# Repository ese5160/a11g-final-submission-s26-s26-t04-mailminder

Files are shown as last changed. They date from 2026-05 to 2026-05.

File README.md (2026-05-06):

Review Assignment Due Date (https://classroom.github.com/a/Y5lYn2wb)

# a11g-final-submission

**Team Number:4**

**Team Name:MailMinder**

| Team Member Name | Email Address | GitHub Username |
| --- | --- | --- |
| Haoliang Xie | liang027@seas.upenn.edu | socold729 |
| Yubin Guan | guan1@seas.upenn.edu | guan1112  |

**GitHub Repository URL: https://github.com/ese5160/a11g-final-submission-s26-s26-t04-mailminder
Git website:https://ese5160.github.io/a11g-final-submission-s26-s26-t04-mailminder**

## 1. Video Presentation
https://youtu.be/0NLSgTLzU24?si=XQApfhHq24TX3WXG

## 2. Project Summary
- Give a 2 sentence description of your device.
  MailMinder is a smart mailbox system built around the SiWG917 Cortex-M4 microcontroller with a custom-designed PCBA, FreeRTOS-based firmware, and cloud connectivity. It detects mail delivery, monitors mailbox security, and allows both local and remote access through keypad input, MQTT communication, and a Node-RED dashboard.
- What inspired you to do the project? What problem is your device solving?
The mailbox in my apartment does not provide any notification when new mail arrives, so we have to check it in person regularly. I often forget to do that, which leads to mail accumulating and sometimes missing important letters.
- How do you use the Internet to augment your device functionality?
The mailbox connects to the cloud through MQTT over TLS, which enables secure two-way communication between the device and a Node-RED dashboard. This Internet connection allows remote unlock commands, temporary passcode updates, real-time status reporting, alert notifications, and OTA firmware updates.
- Explain how your Internet-connected device is designed.
  MailMinder is built as a layered embedded system with custom hardware, FreeRTOS firmware, and cloud integration. On the hardware side, we designed and fabricated a custom PCB centered on the SiWG917 Cortex-M4 MCU and integrated multiple sensors, a keypad, a display, and an electronic lock actuator. On the firmware side, we implemented a multitasking architecture using FreeRTOS, where different tasks handle sensing, local user input, state management, actuator/display control, cloud messaging, and OTA support. On the cloud side, the device communicates with a Node-RED dashboard over MQTT, allowing the mailbox to synchronize status and receive remote commands.
- Include sensors, actuators, and other critical components.
  The system includes several key sensing and control components:
    - IR sensor for mail delivery detection
    - FSR for confirming mail insertion events
    - Reed switch for mailbox door open/close detection
    - IMU for tamper detection and physical disturbance monitoring
    - Matrix keypad for local PIN entry and user interaction
    - Servo/electronic lock for secure locking and unlocking
    - LCD display for local status feedback
    - Wi-Fi / MQTT stack on the SiWG917 for Internet connectivity
    - Custom-designed PCB/PCBA for integrating all system modules into a single embedded platform
- Include your system-level block diagram here.
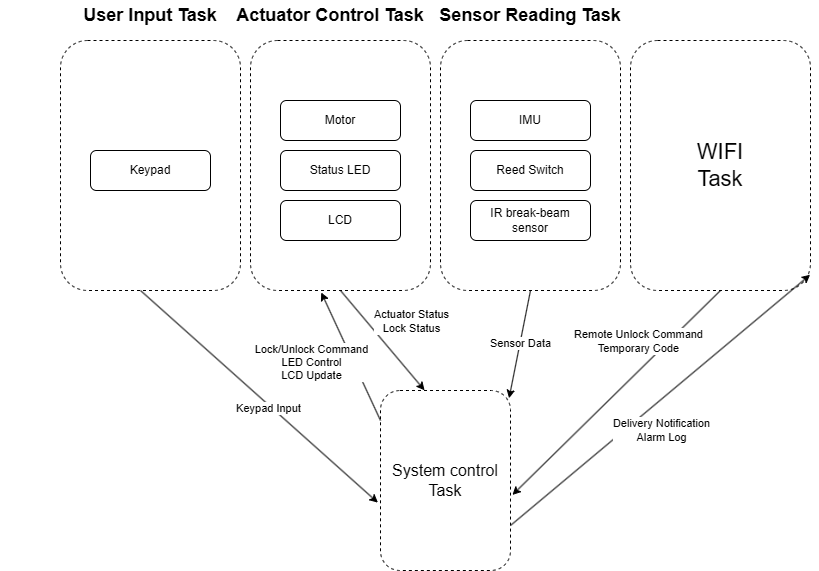
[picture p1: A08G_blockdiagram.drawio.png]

- Where did you face difficulties? This could be in firmware, hardware, software, integration, etc.
  - Hardware1: GPIO56 was originally designed for the LCD MOSI line, but we later found that it was actually configured as MISO.
  - Hardware2: GPIO26 had a pin multiplexing conflict. We intended to use it only as the pin for Keypad 3, but GSPI automatically assigned GPIO26 as the MISO pin.
  - Hardware3: Keypad C1–C4 were floating. When a logic analyzer was attached, the key press signals were stable and could be triggered reliably. However, without the logic analyzer connected, the keypad scanning became very unstable.
  - Hardware4: The IR sensor pin was originally assigned to GPIO50, but it was found to interfere with firmware flashing.
  - Hardware5: The original GPIO could not be multiplexed as a PWM output.
  - Software1: The SPI interface sometimes entered a busy state.
  - Software2: The network stack could easily get stuck during initialization.
  - Software3: During integration testing, the system could experience MQTT disconnection or even program hangs after a long period of inactivity, and the network initialization phase was also prone to getting stuck.
- How did you overcome these challenges?
  - Hardware1: We changed it to GPIO57. 
  - Hardware2: We removed the MISO multiplexing on GPIO26.
  - Hardware3: We connected ground through 18 kΩ pull-down resistors to Keypad C1–C4.
  - Hardware4: It was reassigned to GPIO8, with an external 4.7 kΩ pull-up resistor to 3.3 V.
  - Hardware5: We changed it to ULP_GPIO5.
  - Software1: This issue was addressed by switching or adjusting the configuration to use DMA.
  - Software2: To address this, we designed a reconnection mechanism and placed the network handling in a dedicated task, so that it would not block the execution of other tasks.
  - Software3: At first, we suspected a stack overflow, so we checked the remaining stack space using the high-water mark and printed it for debugging, but this did not appear to be the cause. Later, we suspected that cumulative delays over a long runtime might have caused timing issues or disorder in task scheduling.
- What would you do differently if you had to build this device again?
  We will carefully check the pin assginments and redesign the 3D model.
- What steps are needed to finish or improve this project?
  The model should be refined, especially for the hinges. For the improvement, the way to detect the input of keypad coule be more efficient. And OTA can be improved by using differential updates to increase upgrade efficiency.
- What did you learn in ESE5160 through the lectures, assignments, and this course-long prototyping project?
  I gained hands-on experience with PCB design, which I have never exposed to before. I learned bootloader, FreeRTOS, OTA and so on. Also I learned how to better work with others, how to overcome the problems I have never met before, and how to present your product to other people.
- Provide a URL to your Node-RED instance for our review (make sure it’s running on your Azure instance!)
http://4.246.123.148:1880/
- Provide the share link to your final PCBA on Altium 365.
 https://upenn-eselabs.365.altium.com/designs/AE5C7E01-FBAF-4B34-BA73-49544CBC40D7
## 3. Hardware & Software Requirements
- HRS-01: The FSR sensing subsystem shall detect an added load equivalent to ≥ 10 g placed on the mail tray as a distinguishable change at the ADC input.
    Result: We didn't use it because FSR seemed can only detect concentrated weight. The letter's area is way larger than the FSR's, so it can hardly detect the letter. 
- HRS-02: The door state sensor shall detect the door open/close with a mechanical gap of ≤ 10 mm between magnet and sensor at the "closed" position.
    Result: We tested it and the sensor met the requirment.
- HRS-03 The IMU hardware shall support 3-axis acceleration measurement with selectable full-scale range of at least ±2 g and provide either data-ready/interrupt output or continuous readout capability.
    Result: We tested it and the sensor met the requirment.
- HRS-04 The servo lock actuator shall be able to move between "locked" and  "unlocked" mechanical positions with a rotation range of ≥ 60°.
    Result: We tested it and the sensor met the requirment.
- HRS-05 The device shall include an audible or visual annunciator capable of producing ≥ 55 dBA at 10 cm (buzzer) or a clearly visible status indicator LED.
    Result: We discarded this because we thought this is unnecessary since we have email notifications.
- HRS-06 The hardware shall include an MCU capable of interfacing with required peripherals through I2C, SPI, PWM, and GPIO.
    Result: We tested it and confirmed that the MCU supported all required peripheral interfaces.
- HRS-07 The device shall include a power architecture capable of operating from a 3.7 V rechargeable Li-ion battery and accepting external USB power for charging and system operation.
    Result: We tested it and confirmed that the device could operate from the battery and accept USB power as intended.
- HRS-08 The power architecture shall provide a regulated 5 V rail and a regulated 3.3 V rail for the actuator, MCU, sensors, and display modules.
    Result: We tested it and confirmed that both power rails operated as required.
- SRS-01 The system shall detect an insertion trigger from the IR break-beam input within 50 ms of beam interruption.
    Result: We tested it and the sensor met the requirment.
- SRS-02: Upon an IR insertion trigger, the system shall open a delivery confirmation window of 2–3 seconds during which it evaluates the FSR change to confirm delivery.
    Result: We discarded FSR as we mentioned before. The led on the cloud would turn green once the IR insertion trigger.
- SRS-03: When delivery is confirmed, the system shall publish a delivery event to the cloud within 5 seconds when Wi-Fi is available. If Wi-Fi is unavailable, the system shall defer transmission until connectivity is restored.
    Result: We tested it and the sensor met the requirment.
- SRS-04: The system shall support offline unlock using a valid locally stored keypad PIN. Upon entry of a valid PIN, the system shall actuate the servo to unlock within 2 seconds, regardless of Wi-Fi connectivity.
    Result: We tested it and the sensor met the requirment.
- SRS-05: The system shall support Remote Unlock. Upon receiving an authenticated remote command, the system shall unlock within 5 seconds when connected to Wi-Fi.
    Result: We tested it and the sensor met the requirment.
- SRS-06: The system shall implement a lockout policy. After 3 consecutive failed PIN attempts, the system shall deny further keypad unlock attempts for 30 seconds and update the failed-attempt count and lockout status for cloud publication.
    Result: We replaced this function with a email notification since it is more practical. After 3 consecutive failed PIN attempts, an email notification will be sent to user's phone, telling fail_attempts reaching 3 times.
- SRS-07 The system shall update the local display at ≥ 2 Hz with at least: Mail Present, Lock State, Door State, Network State, and Lockout Status.
    Result: We tested it and the sensor met the requirment.
- SRS-08 The system shall detect door open and door close state changes and publish corresponding door-state events to the cloud within 5 seconds when Wi-Fi is available.
    Result: We tested it and the sensor met the requirment.
- SRS-09 The system shall generate and publish a lock or unlock event whenever the lock state changes, within 5 seconds when Wi-Fi is available.
    Result: We tested it and the sensor met the requirment.
- SRS-10 The system shall detect tamper conditions and publish a tamper alert event to the cloud within 5 seconds when Wi-Fi is available.
    Result: We tested it and the sensor met the requirment.
- SRS-11 The system shall publish periodic status updates containing at least mail presence, door state, lock state, network state, and lockout status at a configurable interval.
    Result: We tested it and the sensor met the requirment.
- SRS-12 The system shall receive authenticated temporary pickup code updates from the cloud and store them for subsequent keypad-based unlock.
    Result: We tested it and the sensor met the requirment.
## 4. Project Photos & Screenshots
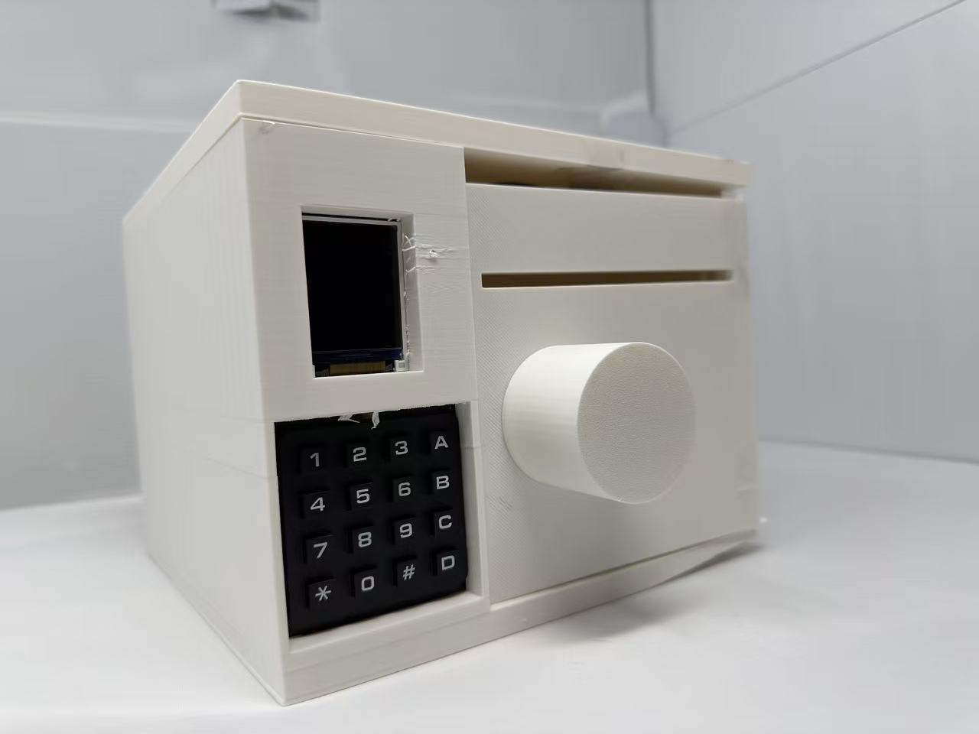
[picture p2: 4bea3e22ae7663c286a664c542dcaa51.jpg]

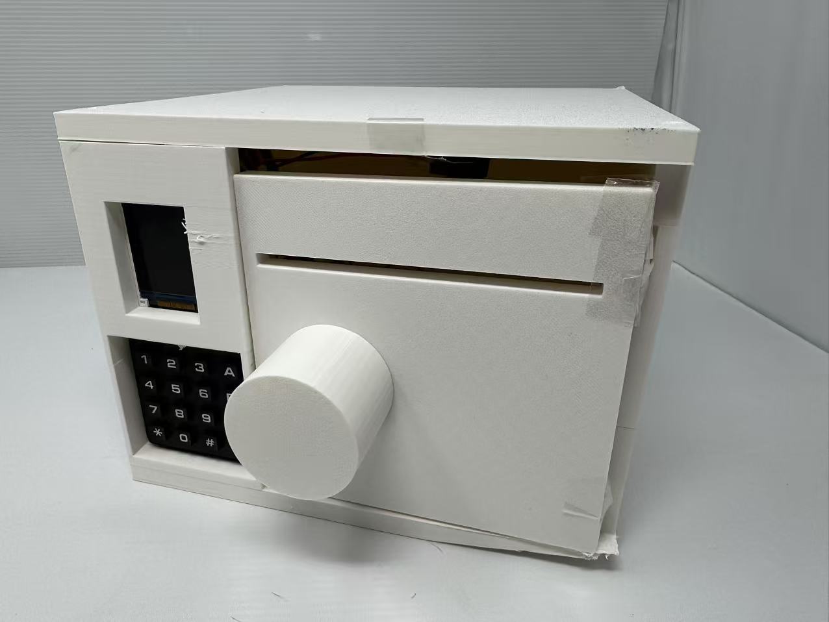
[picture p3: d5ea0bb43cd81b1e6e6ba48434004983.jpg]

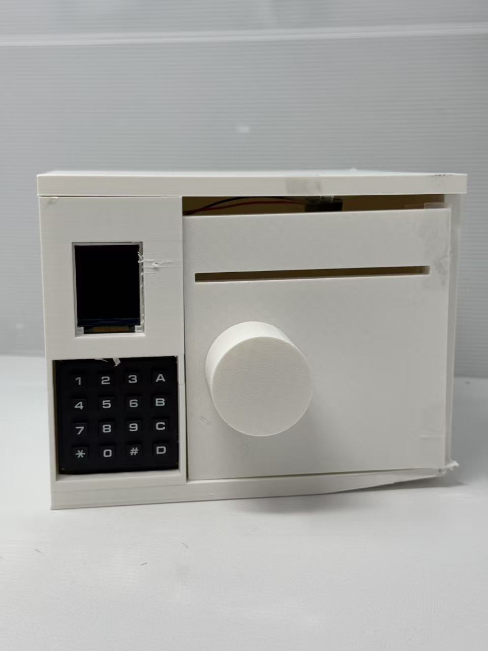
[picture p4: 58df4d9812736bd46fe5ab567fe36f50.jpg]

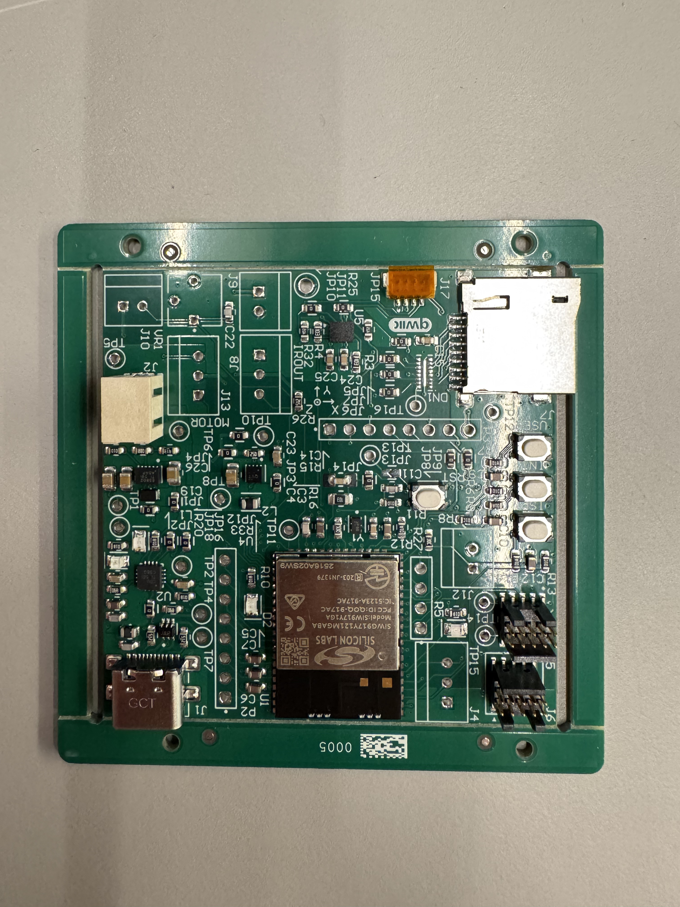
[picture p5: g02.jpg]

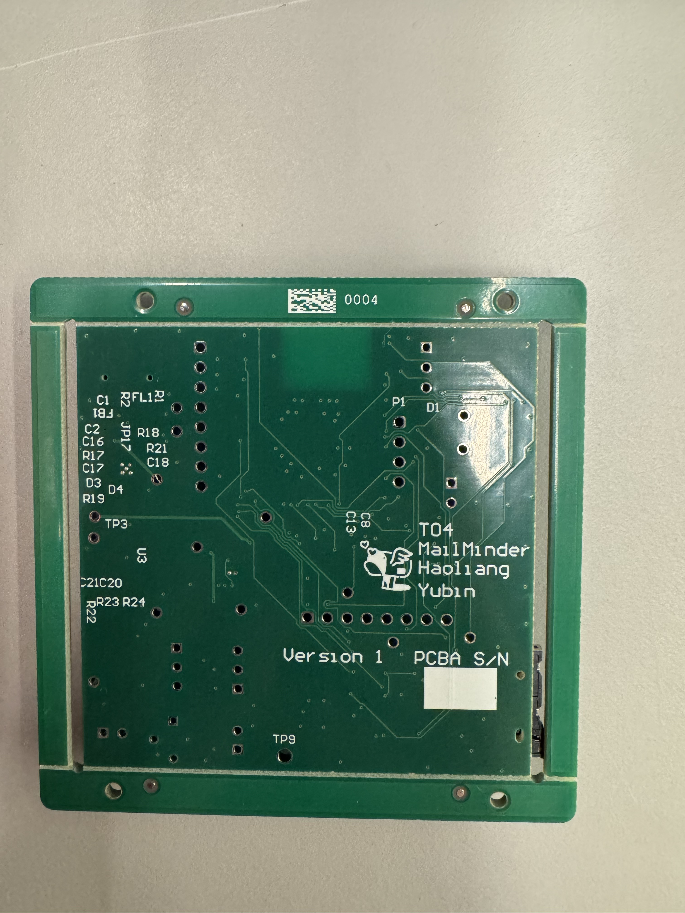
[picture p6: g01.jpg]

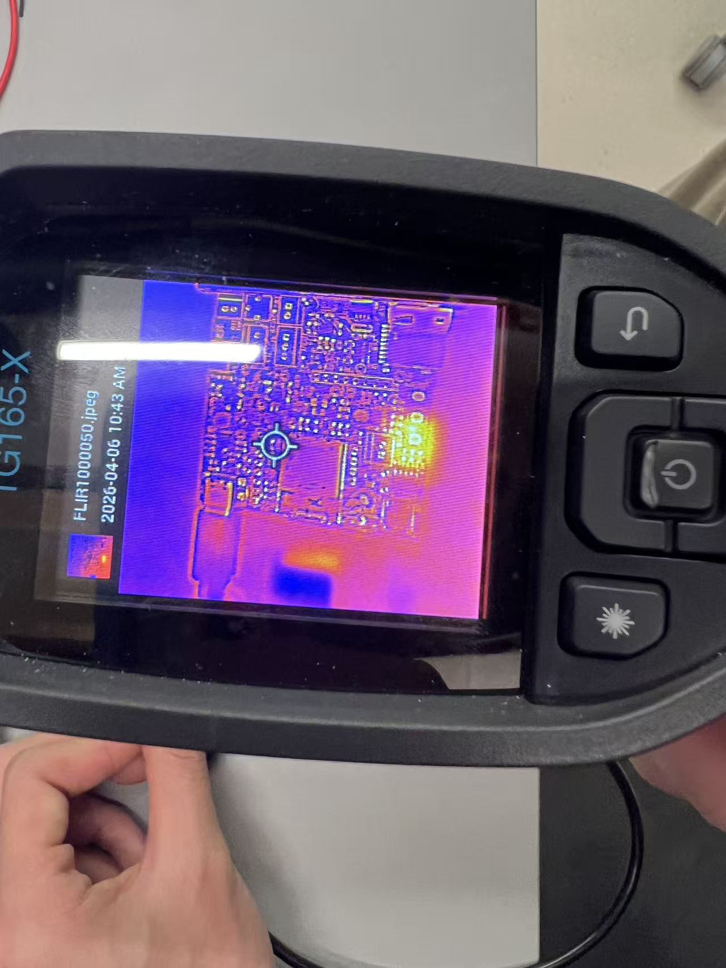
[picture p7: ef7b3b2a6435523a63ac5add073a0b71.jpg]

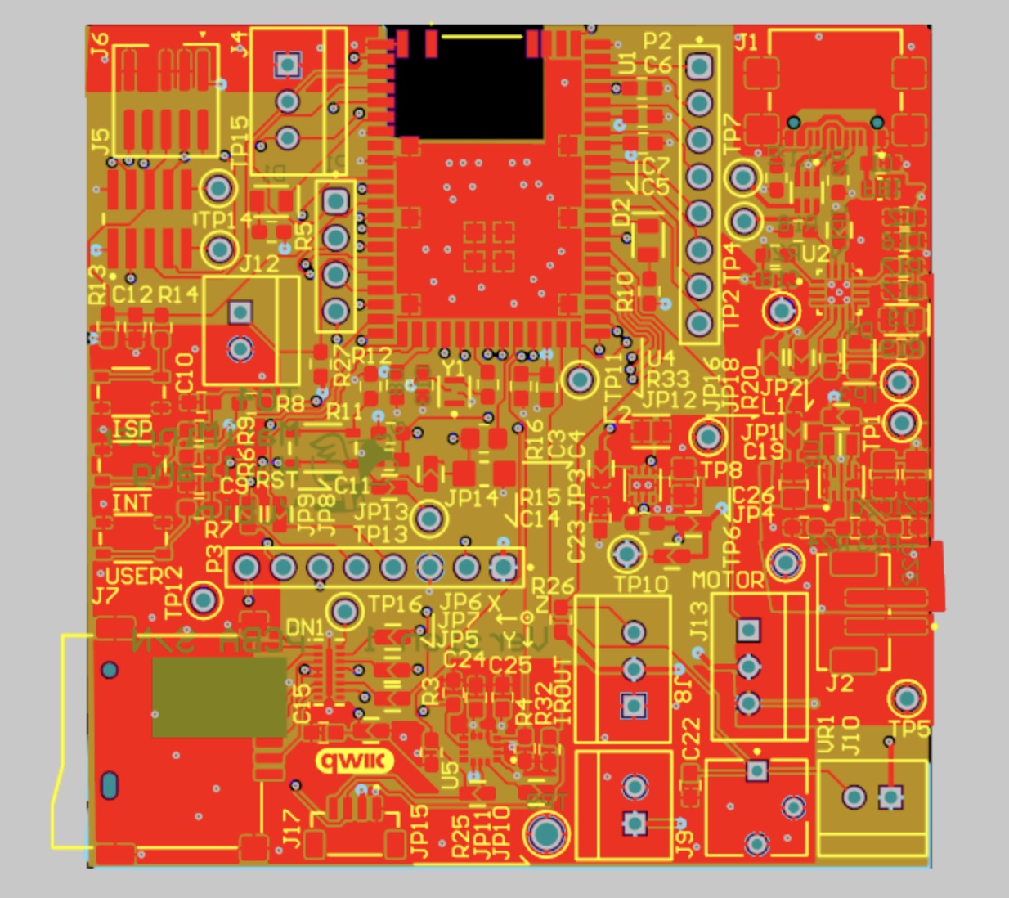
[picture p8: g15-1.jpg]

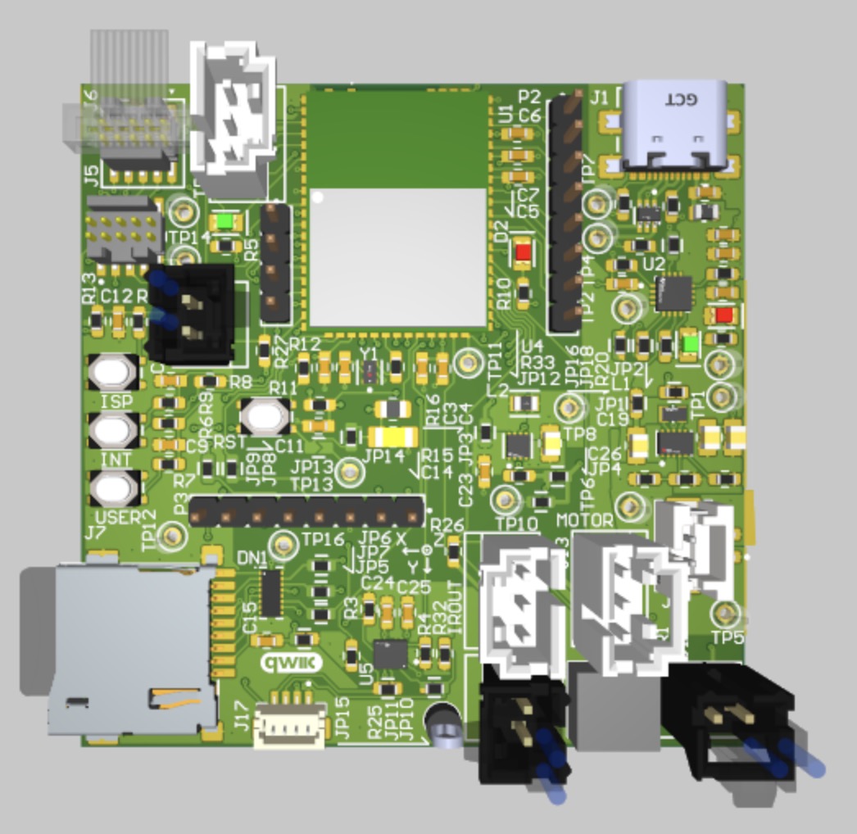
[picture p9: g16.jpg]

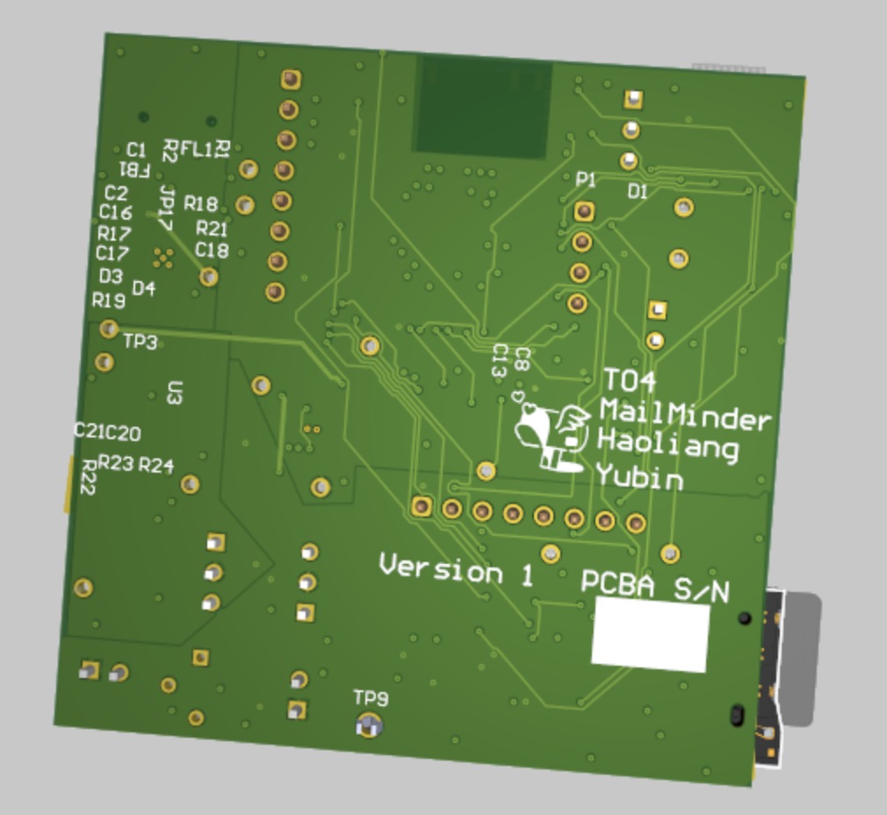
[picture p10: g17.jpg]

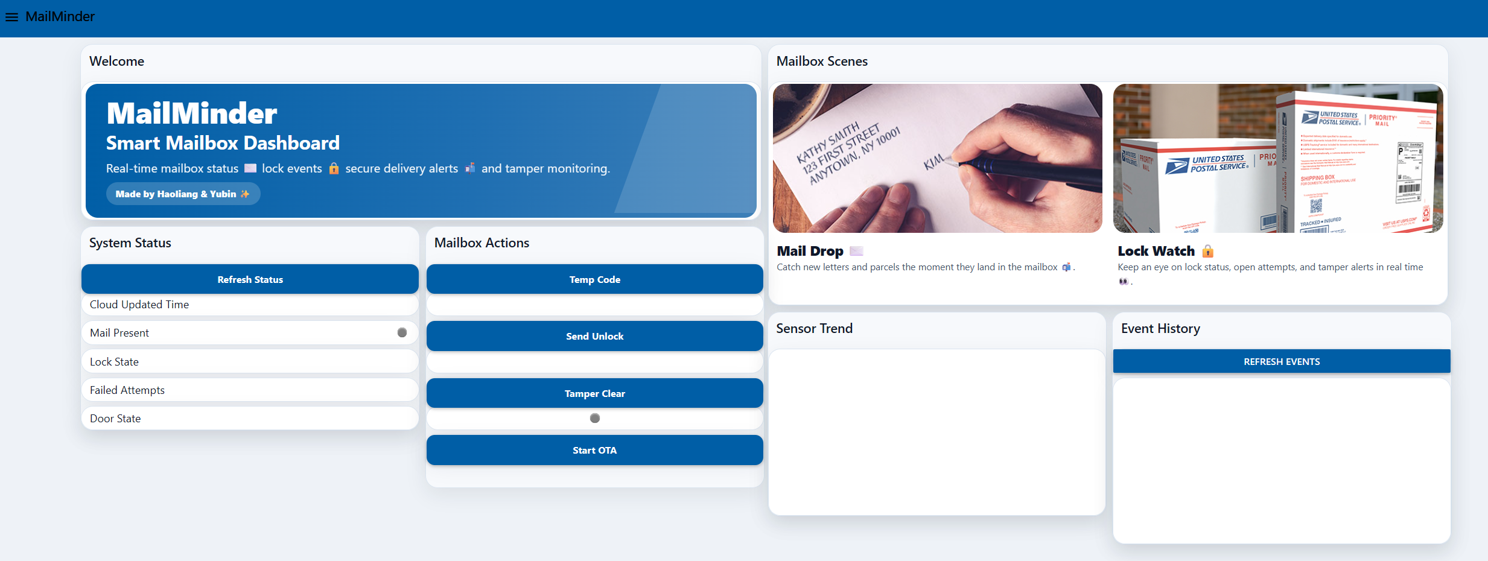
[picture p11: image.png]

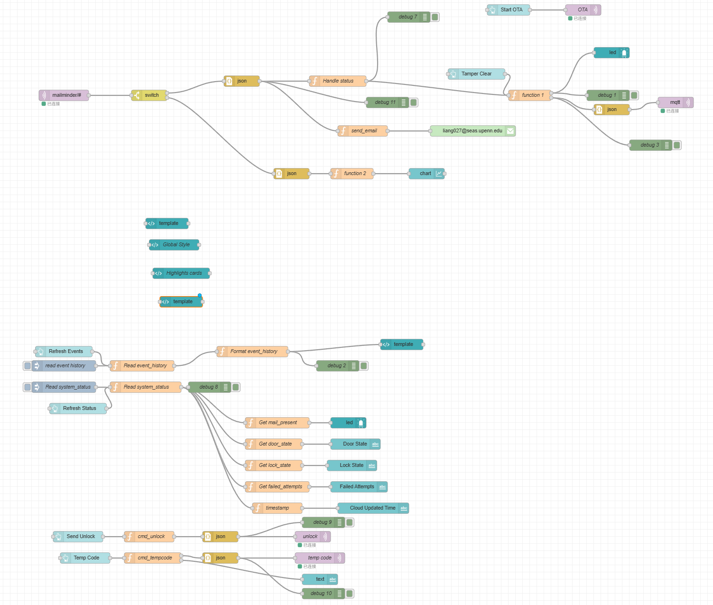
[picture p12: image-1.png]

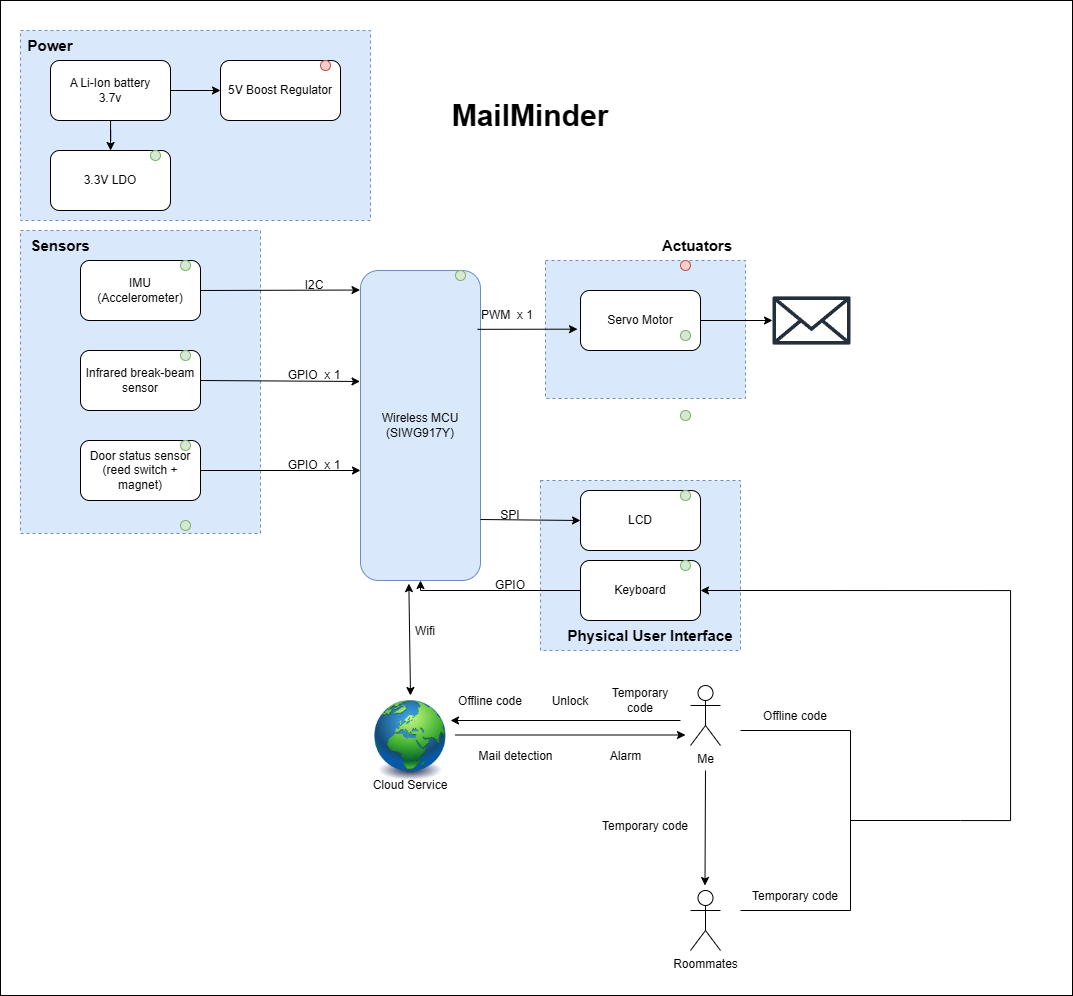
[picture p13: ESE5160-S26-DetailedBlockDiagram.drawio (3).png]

## 5. Codebase

Do *not* commit any of your source code to this repository. Rather, provide links to the other GitHub repository you've already been using with your firmware.

- A link to your final embedded C firmware codebases
  https://github.com/ese5160/final-project-firmware-s26-t04-mailminder/tree/main/0428_sl_final/app/core
- A link to your Node-RED dashboard code
  http://4.246.123.148:1880/#flow/e9cfaa8ead530e0d
- Links to any other software required for the functionality of your device

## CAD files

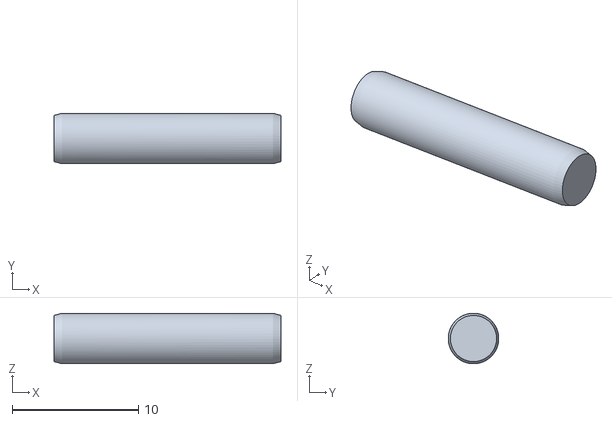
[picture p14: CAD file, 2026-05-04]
MCAD/guan1_ESE5160_Assembly4.STL
18.0 x 4.00 x 4.00

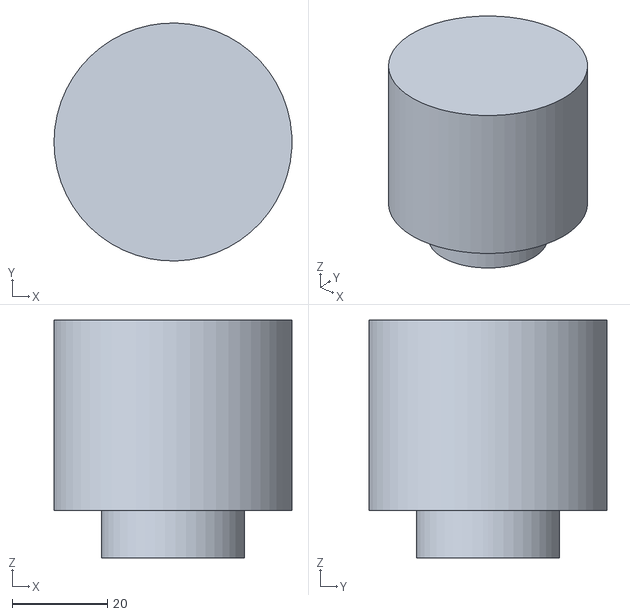
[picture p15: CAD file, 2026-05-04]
MCAD/guan1_ESE5160_conponent4.STL
50.0 x 50.0 x 50.0

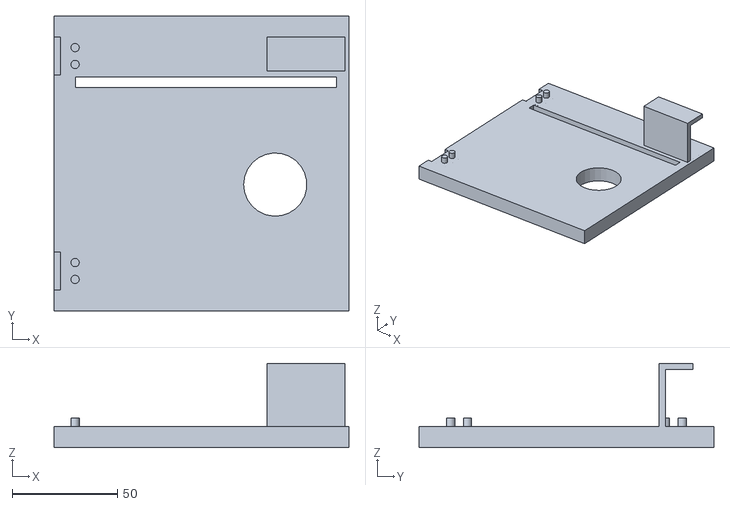
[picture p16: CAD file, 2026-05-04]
MCAD/guan1_ESE5160_component3_new.STL
140.0 x 140.0 x 40.0

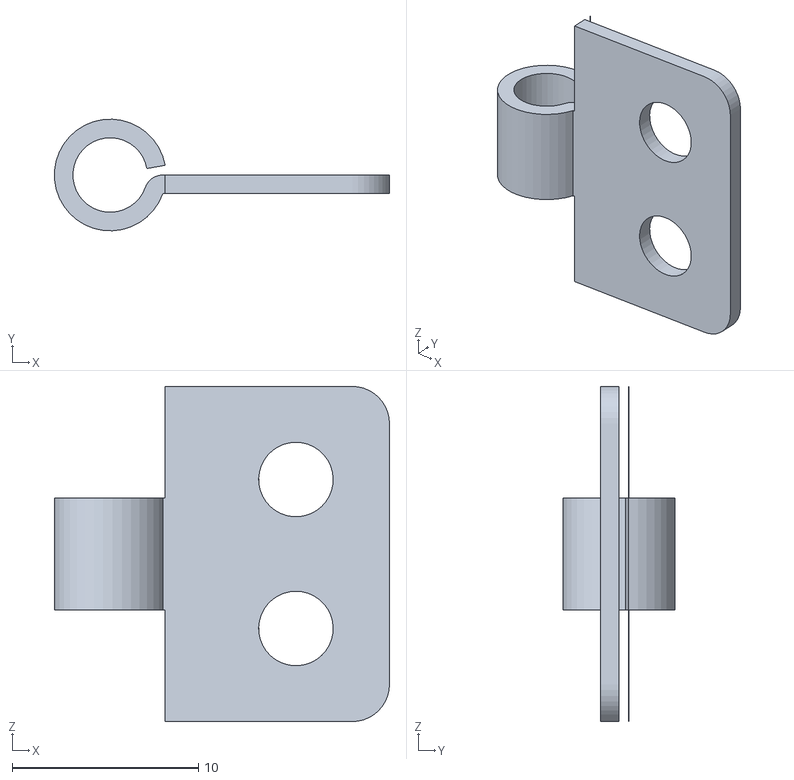
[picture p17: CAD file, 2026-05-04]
MCAD/guan1_ESE5160_hinge1.STL
18.0 x 5.99 x 18.0

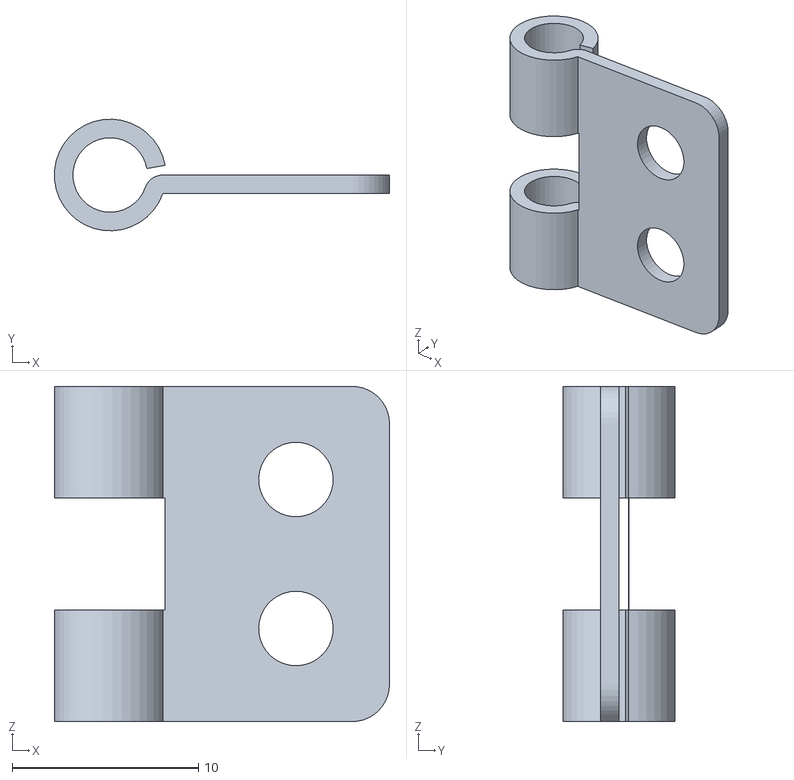
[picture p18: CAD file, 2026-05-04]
MCAD/guan1_ESE5160_hinge2.STL
18.0 x 5.99 x 18.0

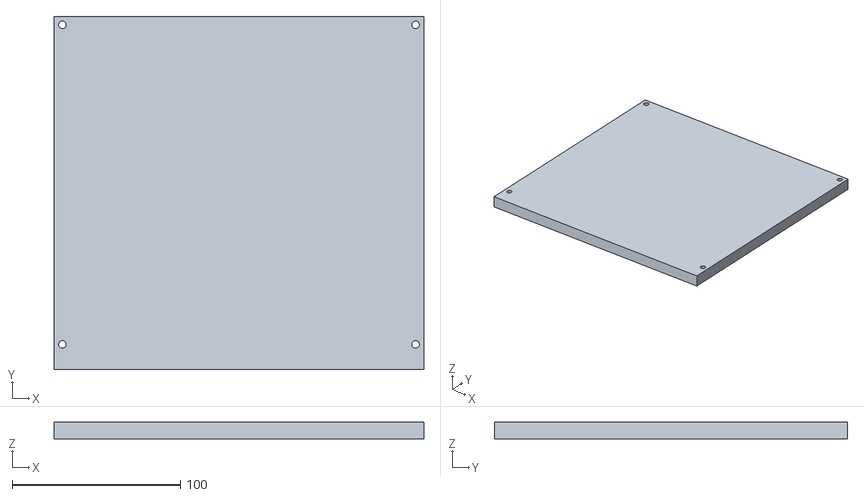
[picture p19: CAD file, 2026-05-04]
MCAD/guan1_ESE5160_component2_new.STL
220.0 x 210.0 x 10.0

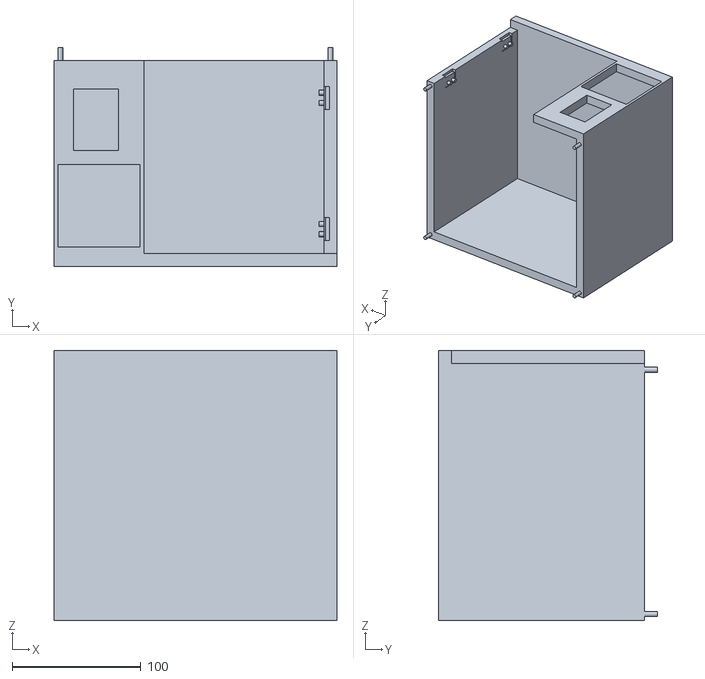
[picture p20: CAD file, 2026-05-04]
MCAD/guan1_ESE5160_conponent1.STL
220.0 x 170.0 x 210.0
